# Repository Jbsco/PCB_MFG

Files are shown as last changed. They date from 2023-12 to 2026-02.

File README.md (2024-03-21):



# PCB_MFG

This repository was created for working with and improving the on-campus PCB design and production process using open-source software resources as well as physical resources and space provided by the University of Colorado Boulder and Colorado Mesa University Partnership Program on the Colorado Mesa University campus. These resources are made available to students and faculty alike.

## Introduction

PCB production is in the process of being made more accessible to students and faculty. Desktop CNC machines are available in labs at Confluence Hall which have the capacity to produce good quality single-sided designs, as well as double-sided designs (with some additional effort), with low/no cost for students and faculty. Efforts have been made to reduce complexity and improve ease-of-use by developing a consistent and repeatable process that produces usable results in a shorter time-frame than ordering from third-party prototyping services.

## Participation

Student and faculty participation in this repository is encouraged! Please check the  and <a href="../../issues">Issues</a> pages to learn about proposed changes and additions. Your engagement in development of this process is welcome. Feedback is also appreciated!
A great way to get started with new commits is to fork this repository, make your changes, and create a pull request to merge changes back into the main branch (pending approval). [Workflow actions](https://github.com/Jbsco/PCB_MFG/actions) are enabled to help enforce spell checking, this uses the [Check-Spelling](https://github.com/marketplace/actions/check-spelling) action.

## Hardware Used

The CNC machines located in Confluence Hall labs are being made available for specific projects by faculty permission, and may be made more widely available in the future. Discuss access with faculty and ensure thorough understanding of the equipment, materials, and lab policies before use - you will gain valuable assistance and knowledge to improve your results and ensure that these resources remain effective and safe for use.

### Genmitsu 3018 Pro Desktop CNC Machines

A 3D-printable fixture which fits 100x70mm copper-clad boards is provided as an STL file in this repository. This was designed specifically for this CNC machine and this process. It provides an easy clamping method with consistent repeatability.

<p align="center">
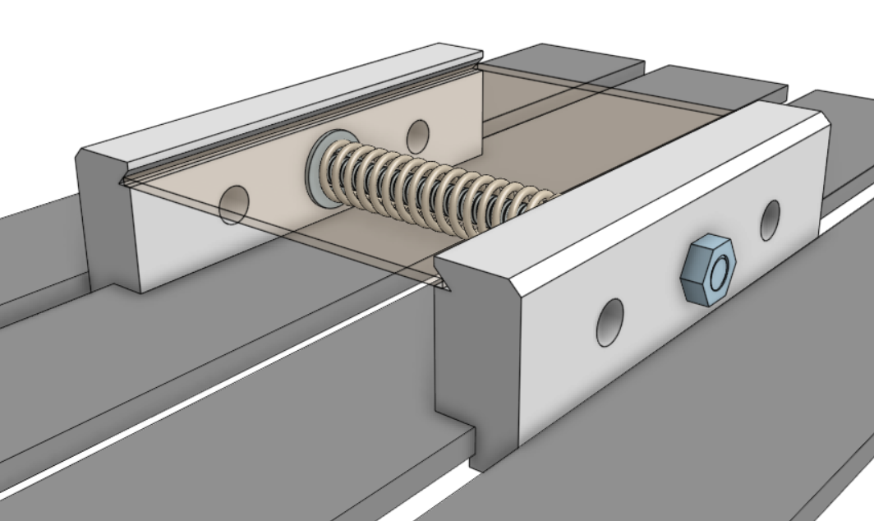
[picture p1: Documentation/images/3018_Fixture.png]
100x70mm Fixture Design
  
</p>

## Software Used

The following software is available on GitHub or their respective web sites, and each were found to be effective for each part of the process detailed within this repository. System compatibility and ease-of-use were priorities, as was open-source status.

* [**Candle**: CNC control and heightmapping software (Windows or Linux)](https://github.com/Denvi/Candle)

* **FlatCAM**: Gerber & Excellon intake, toolpathing, and Gcode output (Windows, Linux, MacOSX) ***comprehensive alternative to Inkscape & jscut***
  * [FlatCAM BitBucket](https://bitbucket.org/jpcgt/flatcam/src/master)
  * [FlatCAM Docs](http://flatcam.org)

* **KiCAD**: Schematic & PCB design software, simulation, Gerber & SVG output (Docker, Windows, Linux, MacOSX)
  * [KiCAD GitHub](https://github.com/KiCad)
  * [KiCAD GitLab](https://gitlab.com/kicad)

Originally, Inkscape and jscut were used to create Gcode files using SVGs, rather than Gerber files. This tested poorly among students, so FlatCAM is preferred, but this process is retained below the current process for posterity.

* **jscut**: SVG intake, toolpathing, and GCode output (in-browser)[
  * [jscut GitHub](https://github.com/tbfleming/jscut)
  * [jscut](https://jscut.org) 
* [**Inkscape**: SVG preparation for jscut (Windows, Linux, MacOSX) ](https://github.com/inkscape/inkscape)

## Process

It is recommended to have access to the above software. As they have their own release channels please refer to their documentation. Generally, Candle, FlatCAM, and KiCAD are installed software, and releases are available from their respective sites. Linux installs for common distributions are often available.

Arch Linux users are recommended to install `candle-bin` from the AUR using `yay`, while FlatCAM runs from source using `python FlatCAM.py` after installing dependencies (`python-vispy` 0.7 or lower is needed. FlatCAM can also be installed as `flatcam-git` from the AUR using `yay`, but the dependency `python-svg.path` may need to be installed with the `--mflags "--nocheck"` flags in order to bypass failed tests), and KiCAD is available using `pacman -Syu kicad` and KiCAD libraries using `pacman -Syu --asdeps kicad-library kicad-library-3d`.

Drivers for the 3018 CNC machine may need to be installed for communication through Candle, these may be found on the Sainsmart site.

Additional documentation (including general usage guides, tips, and tricks) for each application used in this process will be linked within this repo.

## Tutorials

* [Using KiCAD](Documentation/using_KiCAD.md)
* [Using FlatCAM](Documentation/using_FlatCAM.md)
* [Using Candle](Documentation/using_Candle.md)

Originally, Inkscape and jscut were used to create Gcode files using SVGs, rather than Gerber files. This tested poorly among students, so FlatCAM is preferred, but this process is retained here for posterity.

* [Using Inkscape and jscut](Documentation/using_Inkscape_JSCut.md)

## Heightmap Modeling
As a Fall 2023 Intro to Probability Theory final project, a dataset was built from Candle heightmaps and various conclusions were drawn from observations and analysis of this data. Data was interpreted using the MATLAB scripts included in this repository. The resultant report and supporting materials are included in [Reports](/Reports/).

The resultant model heightmap, which is based on the mean data, is available at [/Reports/Code/bootModel.map](/Reports/Code/bootModel.map). This heightmap may prove more useful as the dataset grows.

In the future, other students and faculty will have the opportunity to contribute to the dataset and assist in refining the model.

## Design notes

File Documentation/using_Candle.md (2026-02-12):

# Using Candle

Candle controls the CNC machine directly over USB or by generating a Gcode file for running on a USB stick inserted in the CNC machine.

* Ensure Candle is connected to the CNC machine over USB by selecting "Service → Settings" and "Connection" in the pop-up window. The "Connection" drop-down should show a numbered COM option corresponding to the CNC machine - if not, verify the correct drivers have been installed.

* Close this window and observe the control panel, which may be configured by adjusting settings.
The 3018 Pro CNC machine is capable of making use of the probe and heightmap functions in Candle, which are critical to producing good quality PCB designs.

* In order to use the continuity probe, where the cutting tool making contact with the PCB surface triggers the probe stop, GRBL commands must be sent to the machine via the command terminal, and the tool head spindle must be connected to a "GND" pin on the control board, and the PCB must be connected to the "A5" pin on the control board. Some 3018 Pro machines shipped with different labelling on the control board - the pins may also be labeled "probe". Both types of control boards are present in the campus labs, so please be aware of this if you use different machines. These connections are easily made using alligator clips and pin headers. These connections must be removed when turning the spindle on - **be sure to always check and check again that these clips are removed from the spindle before turning the spindle on**.

* The GRBL commands that must be sent to properly set the homing cycle for continuity probing are `$22=1` (homing cycle enable) and `$23=0` (homing cycle direction). Additional GRBL commands are provided in the "GRBL_Settings_Pocket_Guide_Rev_B" document or at www.DIYMachining.com/GRBL.

* With the homing cycle configured, spindle off, and clips attached, use the control panel to raise the tool head and position the cutting tool over a corner of the PCB. Note the directionality of all controls, and observe the Candle graphical display of the tool head.

* The Z-probe button may be used to slowly lower the tool head until continuity is made and the tool head stops. Zero the machine in Candle by selecting the Zero X, Y, and Z buttons in the control panel.

* Load the Gcode file generated by FlatCAM by selecting "File → Open". Select the contour CNC job.

<p align="center">
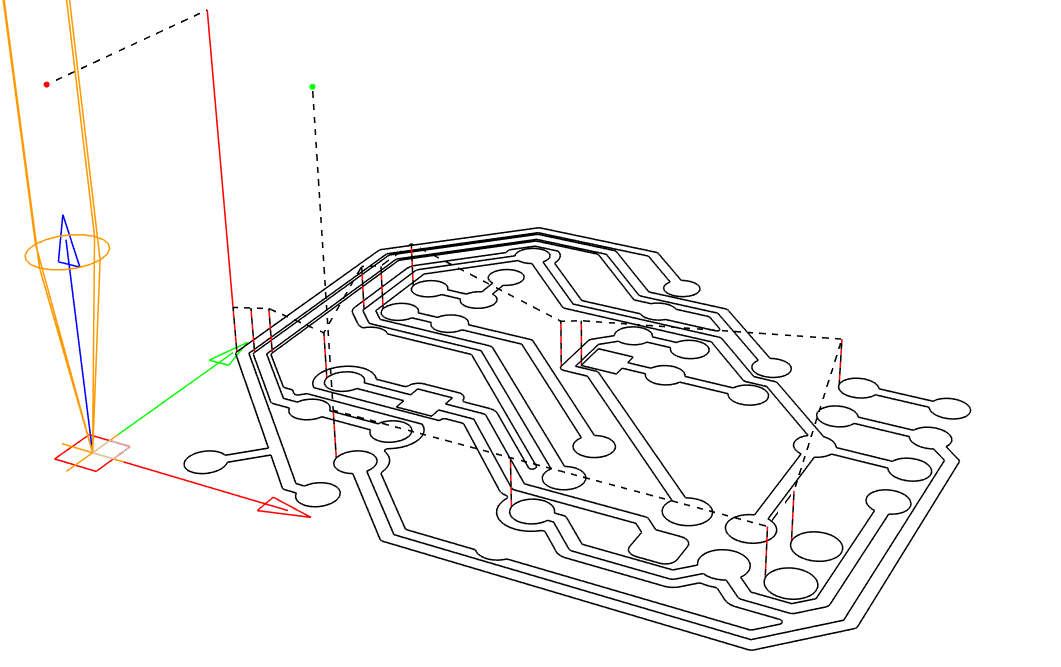
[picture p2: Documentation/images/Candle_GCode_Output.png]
Example Gcode File Loaded in Candle
  
</p>

* Once a Gcode file is opened, Candle enables the Heightmap function. Select "Create" (or optionally apply the modeled heightmap that was developed for rapid prototyping using the fixture design included in this repository).

* Adjust the Heightmap settings to enclose the design shown in the graphical window, or select the "Auto" button to automatically set parameters.

* Select reasonable values for the Heightmap Probe Grid. Some parameters may be unfamiliar - "F" is the probe feedrate, "Zt" is the distance to raise the tool head when moving to the next point, and "Zb" is the distance to lower the tool head when probing. If the machine was zeroed previously, then a value of 1.50 for Zt with other values left as default is likely sufficient.

* Observe the arrangement of the graphical representation of the operation and visually verify that the machine will not crash before selecting "Probe". The routine will run until complete or stop if continuity was made at an unexpected point. If the Heightmap was not able to be completed, try adjusting the "Zt" or "Zb" parameters accordingly, or inspect for other issues, before trying again.

<p align="center">
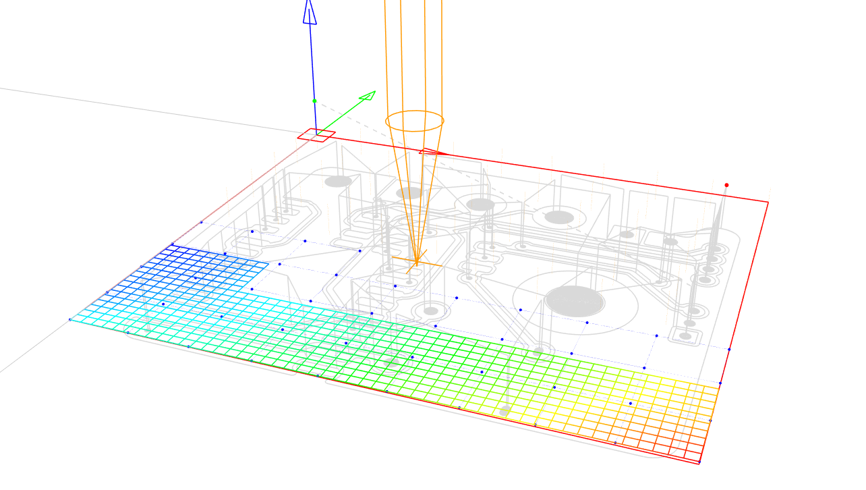
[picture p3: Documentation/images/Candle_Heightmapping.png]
Example Candle Heightmap Routine Being Performed
  
</p>

* With the Heightmap complete, close the Heightmap mode by selecting "Edit", and select the checkbox "Use Heightmap".

* Raise the tool head slightly and reset alarms if necessary.

* Perform additional visual checks to verify the machine will be able to proceed with the milling operation unobstructed, and **remove clips attached to the spindle and PCB before turning the spindle on**.

***Note that the spindle rotates near 10,000 RPM, and the cutting bit could break and create a dangerous situation. Follow lab policies regarding safety and have faculty or senior students familiar with this process verify that everything is in order before turning on the spindle and running milling Gcode.***

* Turn the spindle on and select "Send" to run the operation. Observe the machine safely and while wearing safety glasses.

* The routine should complete and the PCB will be ready for hole drilling operations. Hole drilling operations should be completed without changing the machine zero positioning, or else alignment will be difficult to achieve accurately. The hole drilling operation should be straightforward so long as the tool bit is changed without losing the machine positioning.

<p align="center">
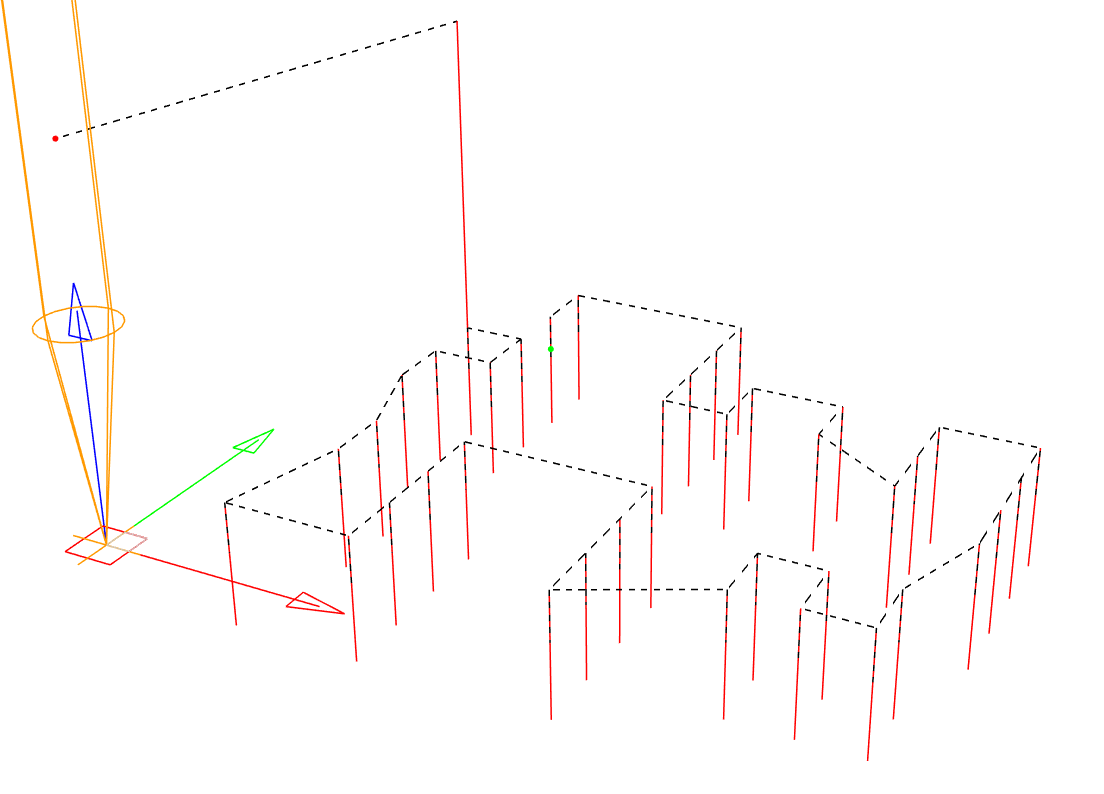
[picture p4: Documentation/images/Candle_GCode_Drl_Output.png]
Example Drill Gcode File Loaded in Candle
  
</p>

The routine should complete and the PCB will be ready for final processing or cutting operations.

<p align="center">
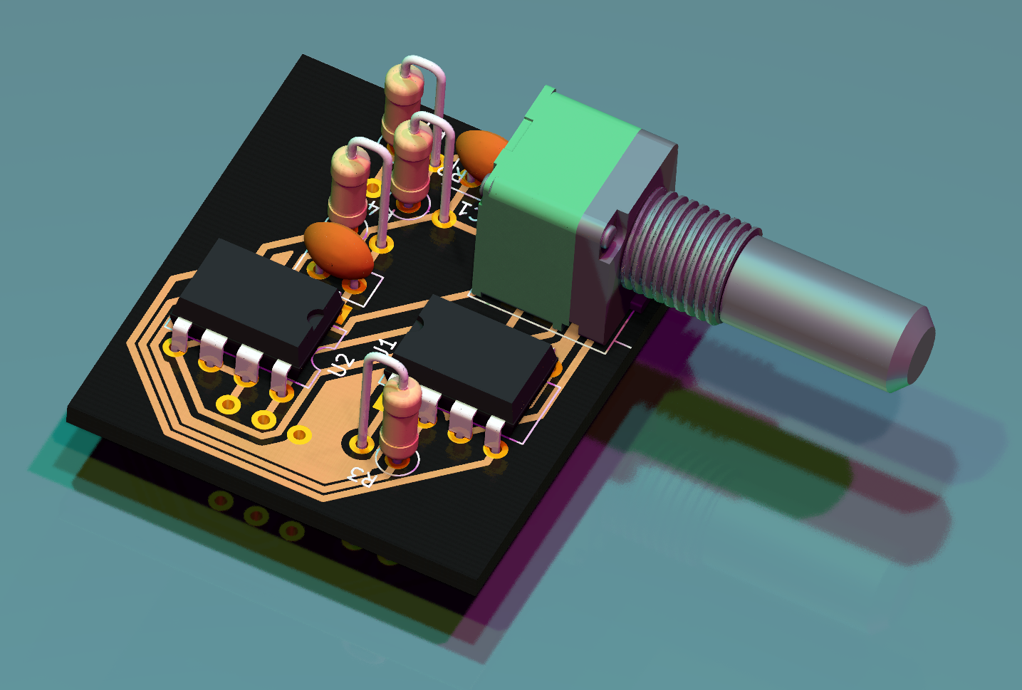
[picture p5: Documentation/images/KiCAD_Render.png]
Example Populated PCB Rendered in KiCAD
  
</p>

Candle Tips (for Genmitsu CNC 3018-PRO): [Tips_Candle_Genmitsu_CNC3018](./using_Candle_GenmitsuCNC3018.md)

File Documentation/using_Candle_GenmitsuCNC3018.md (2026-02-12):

# FlatCAM Tips (for Genmitsu CNC 3018-PRO)

This section provides practical guidelines to reduce common **design and manufacturing issues** when milling PCBs designed in **KiCad** using the **Genmitsu CNC 3018-PRO** CNC machine
([Amazon link](https://www.amazon.com/Genmitsu-3018-PRO-Control-Engraving-300x180x45mm/dp/B07P6K9BL3)).

<p align="center">
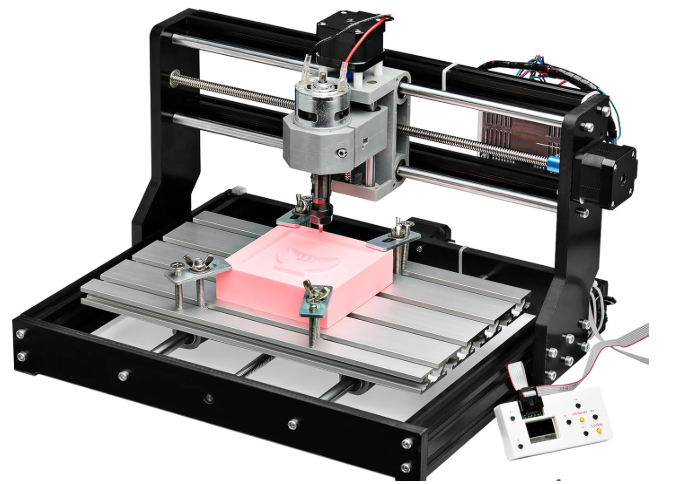
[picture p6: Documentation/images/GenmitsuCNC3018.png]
Genmitsu CNC 3018-PRO
  
</p>

The **Genmitsu CNC 3018-PRO** is an entry-level, desktop, 3-axis CNC router intended for hobbyists, students, and educational environments. It has a working area of approximately **300 × 180 × 45 mm**, uses a 775 spindle motor, and is controlled via **GRBL firmware**.

The machine is commonly used for engraving and light milling of materials such as wood, plastics, acrylic, **PCB copper boards**, and soft aluminum. While affordable and relatively easy to assemble, it is designed for **prototyping and learning**, not industrial-grade PCB manufacturing.

Although the machine offers reasonable precision, PCB milling imposes strict constraints on **trace width, clearance, pad size, and tool depth**. Inadequate settings can easily result in short circuits, broken traces, incomplete isolation, or partially milled pads.

---

# Safety Notes

- Always wear **eye protection**
- Never touch the tool while the spindle is running
- Keep hands away from moving parts

<p align="center">
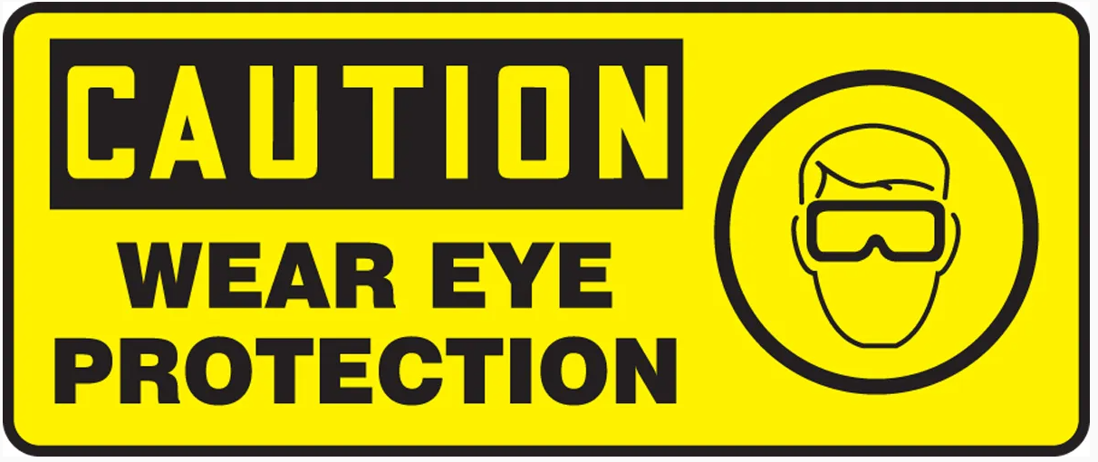
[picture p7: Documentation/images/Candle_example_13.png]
  
</p>

---

# Candle Guidelines for CNC Milling

From **FlatCAM**, three G-code files must be generated:

- `'name'_MILLING_0.075.nc`
  — Used in **Candle** to mill (isolate) the copper traces

- `'name'_DRILLING_0.075.nc`
  — Used in **Candle** to mark the hole centers

- `'name'_DRILLING_2.5.nc`
  — Used in **Candle** to drill the holes through the board

---

# Installing Candle

Download Candle

On Linux, you may need to run:

```bash
sudo ./candle
```

---

# Required Items for This Activity

<p align="center">
  
</p>

- Genmitsu CNC 3018-PRO
- 3D-printable fixture
- USB cable
- Power supply
- Phenolic copper clad board (approx. 10 × 8 cm)
- Milling bit (0.5 mm recommended)
- Drill bit (1.0 mm recommended)
- Z-probe wires (green and white)

---

# Preparing the CNC Machine

- Plug the USB cable into the computer (**do not turn on the CNC machine yet**)
- Open Candle:
  ```bash
  sudo ./candle
  ```

- Ensure the status shows **"Idle"**
  - If not: `Service → Settings → Port`

- Click the **lock button** to unlock the machine
- Press the **emergency button** (so the machine does not move when powered)

<p align="center">
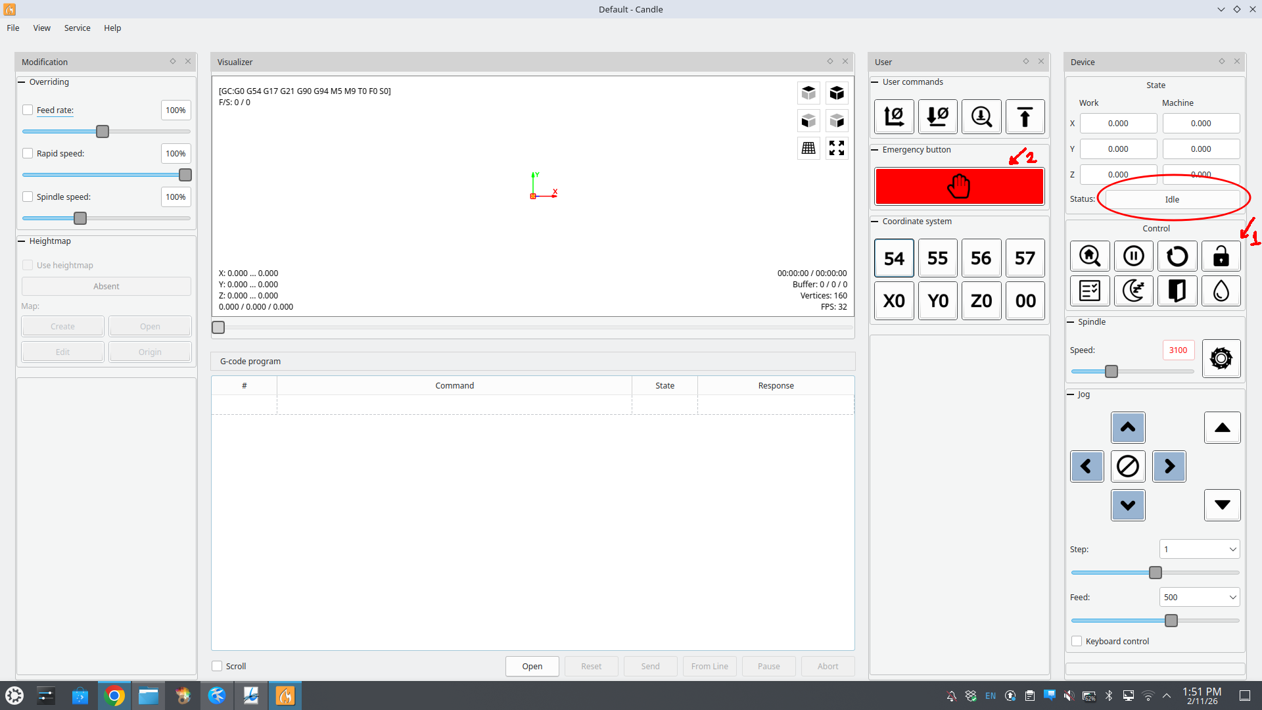
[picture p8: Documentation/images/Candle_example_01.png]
  
</p>

- Plug the CNC machine into the power outlet
  - The machine should NOT move

- Close and Restart Candle

- Ensure status is **Idle**

- Unlock the machine

- You can now move the axes using Candle controls

- Move the spindle to one corner of the machine
  - **Do not exceed machine limits**

- Install the board holder system

<p align="center">
  
</p>

- Place the **phenolic copper clad sheet (10 × 8 cm)**

<p align="center">
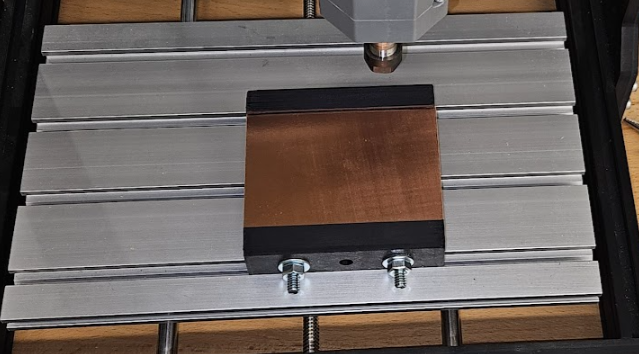
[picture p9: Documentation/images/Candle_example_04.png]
  
</p>

---

# Preparing the Tools

To maintain consistent tool height, mark both tools at the same reference height.

### Tools

- **Milling tool:**
  0.5 mm carbide end mill (1/8" shank)

- **Drilling tool:**
  1.0 mm tungsten carbide PCB drill bit (1/8" shank)

<p align="center">
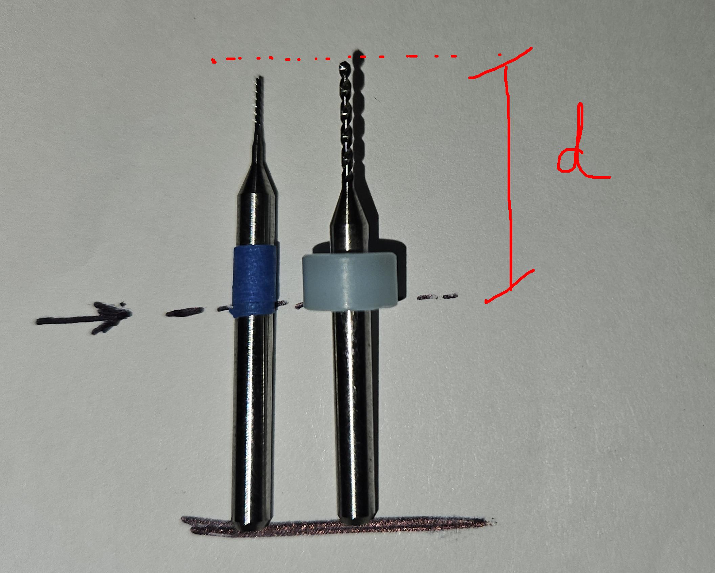
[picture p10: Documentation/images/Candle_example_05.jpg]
  
</p>

- Install the **milling tool** first

---

# Setting the XY Reference (Origin)

- Close and Restart Candle

- Ensure status is **Idle**

- Unlock the CNC machine

- Move the spindle to the **bottom-left corner of the copper board**

<p align="center">
  
</p>

- Set this position as **X = 0, Y = 0**

<p align="center">
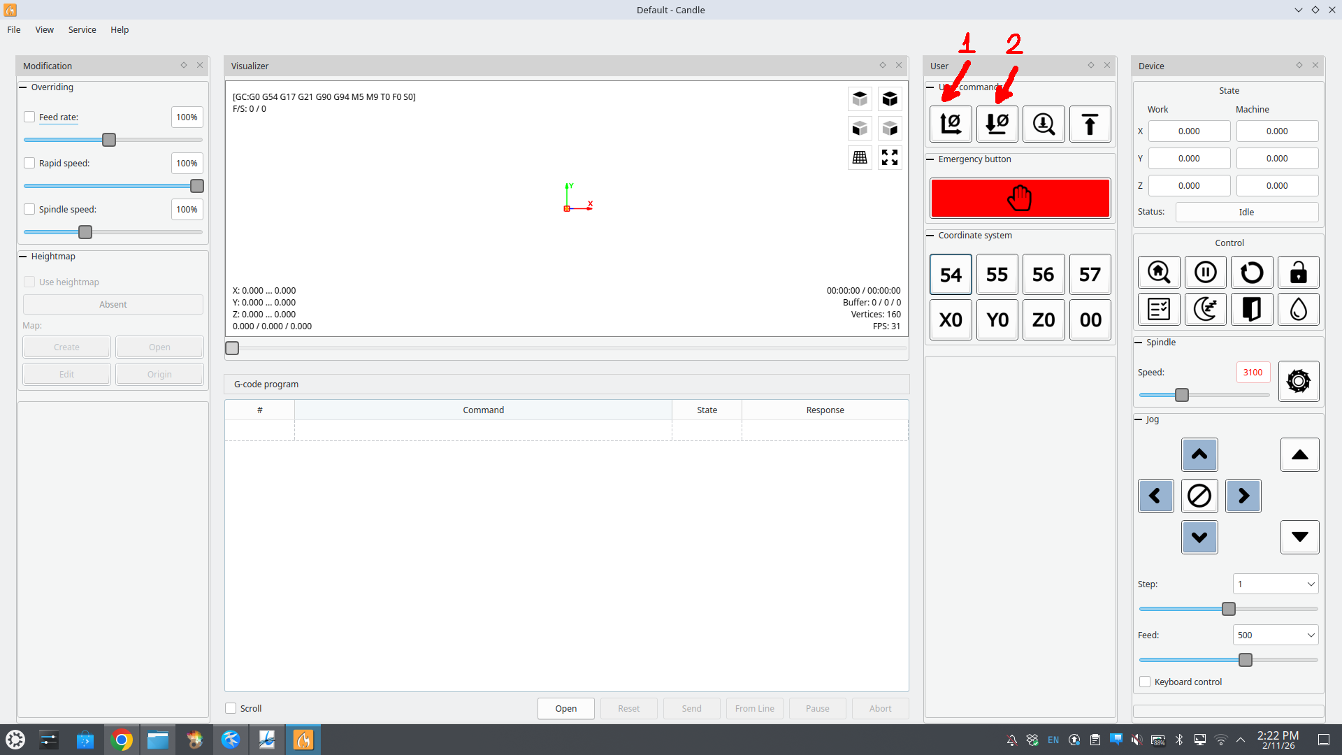
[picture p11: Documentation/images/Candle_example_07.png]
  
</p>

- Close and Restart Candle

- Ensure status is **Idle**

- Unlock the CNC machine

- Set this position as **X = 0, Y = 0** again

- Load the milling file:
  `'name'_MILLING_0.075.nc`

- Set **Safe Z**

⚠ **If the spindle moves unexpectedly, immediately turn off the machine.**

<p align="center">
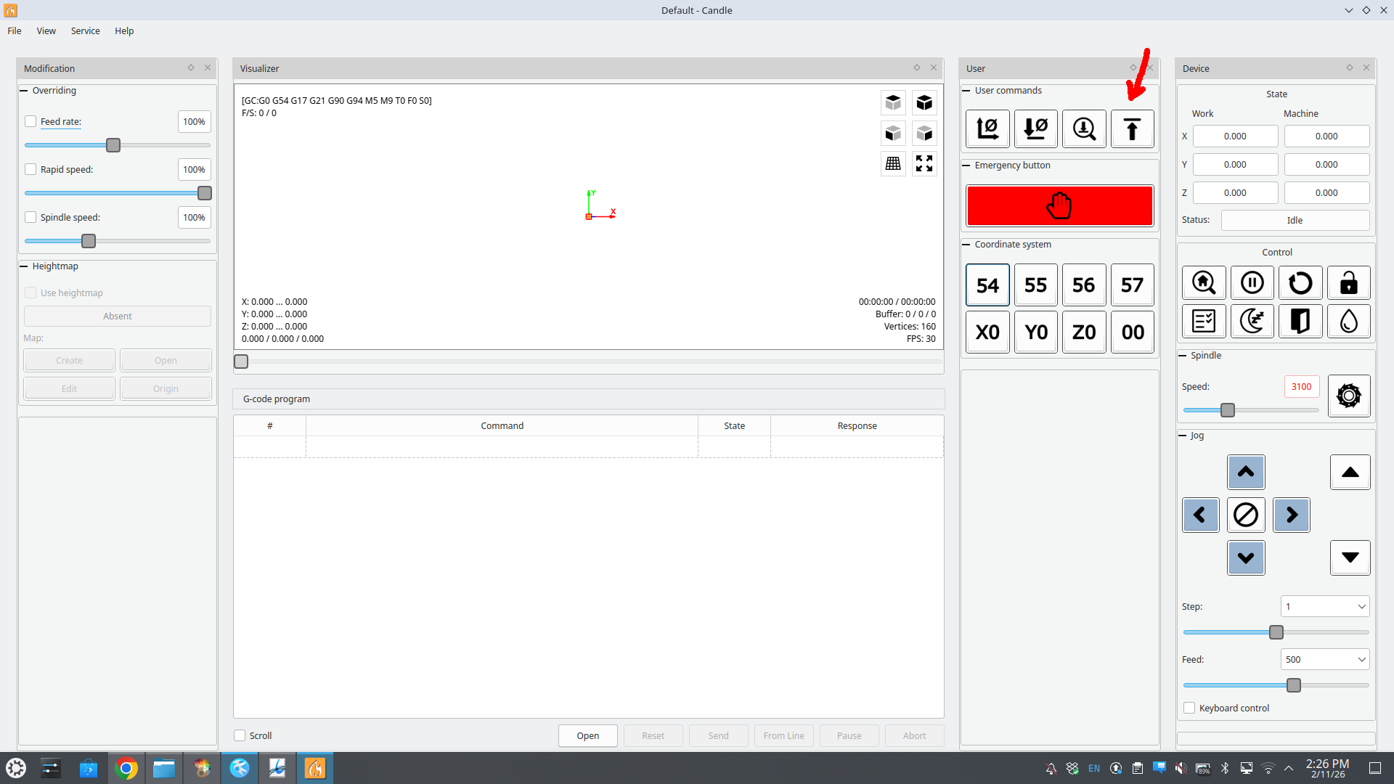
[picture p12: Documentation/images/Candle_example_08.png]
  
</p>

---

# Setting the Z-Probe

Before probing:

- Ensure the two probe cables are connected properly

<p align="center">
  
</p>

- For this setup:
  - **White cable → spindle motor**
  - **Green cable → copper board**

<p align="center">
  
</p>

⚠ **WARNING:**
Improper connection may damage the board or tool.

- Click **PROBE Z**

<p align="center">
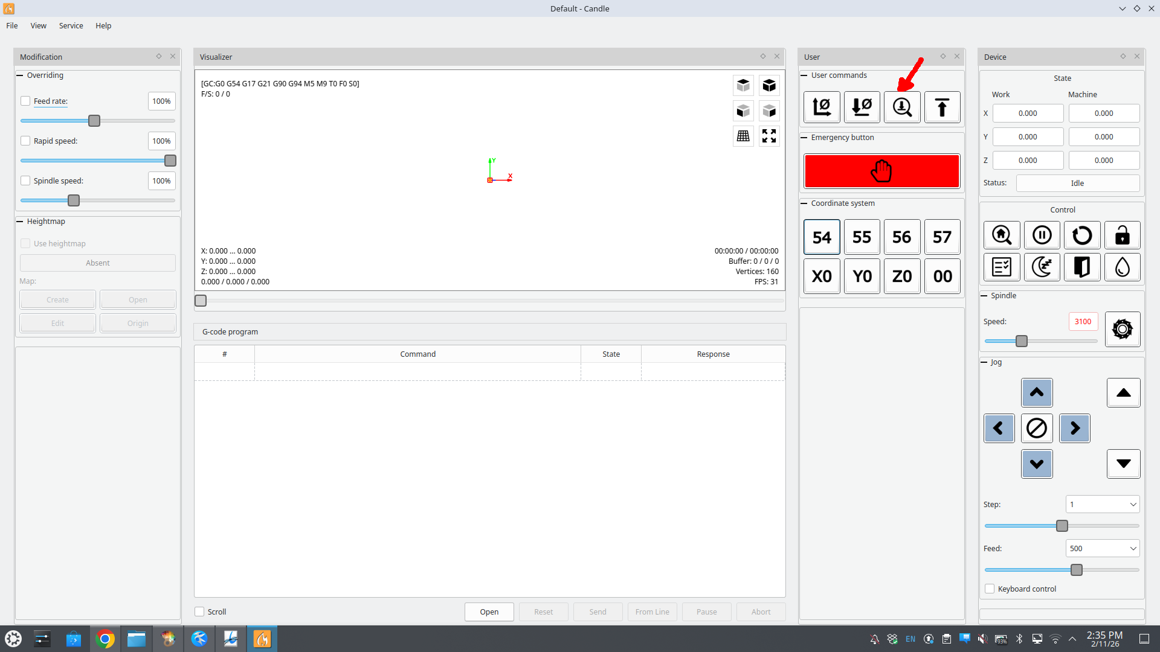
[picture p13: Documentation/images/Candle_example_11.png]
  
</p>

---

# Creating the Heightmap

- Click **Create**
- Click **Auto** (covers only the board area)
- Set:
  - **Zt = 2** (safe probing height)
  - **Zb = -1** (maximum probing depth)

<p align="center">
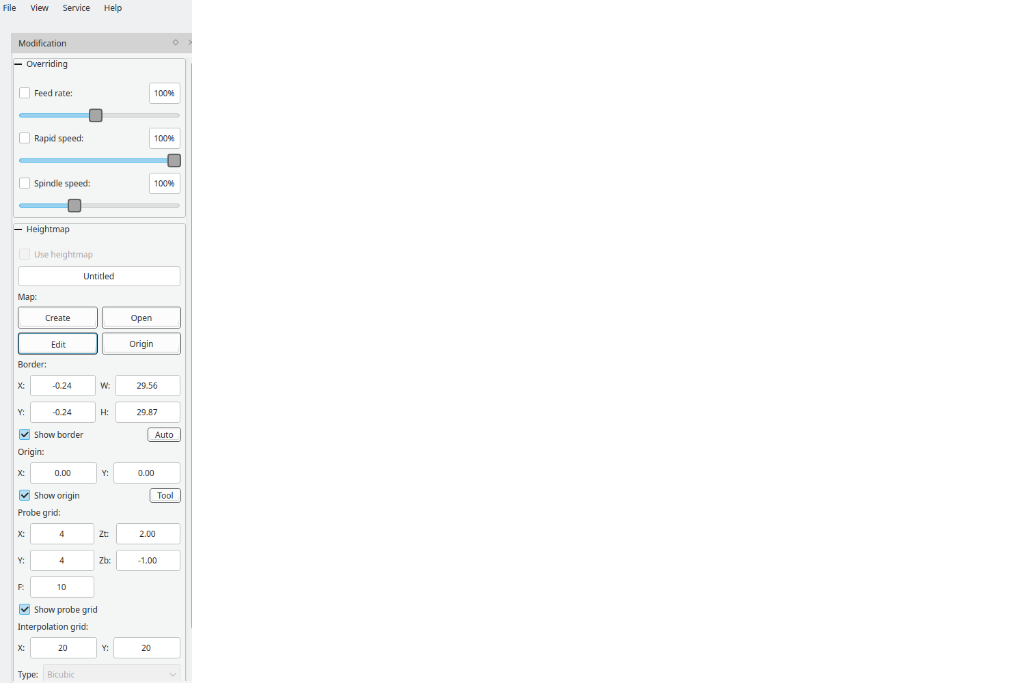
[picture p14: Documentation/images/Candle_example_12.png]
  
</p>

- Click **PROBE**
- When finished, click **EDIT** to return to the main screen

⚠ **Disconnect the white and green probe wires before proceeding**

---

# Using the Heightmap

- Enable **Use Heightmap**

- Set spindle speed (**FEED**) to **3000 rpm**

⚠ Double-check that probe wires are disconnected

- Click **SEND**

The milling process will now begin using surface compensation from the heightmap.

---

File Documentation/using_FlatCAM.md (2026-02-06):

# FlatCAM

* In FlatCAM, open the Gerber and the Excellon files to add them to the FlatCAM project.

<p align="center">
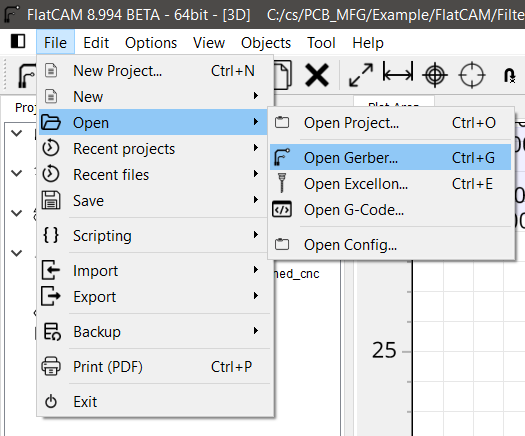
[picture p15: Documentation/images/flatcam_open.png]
FlatCAM Open Dialogue
  
</p>

* These objects may be placed far from the origin, so select all using the "Ctrl + A" shortcut, and Move to Origin using the "Shift + O" shortcut. It is important to select all objects to move them as a group, otherwise the drill objects will not be aligned to the contour objects.

<p align="center">
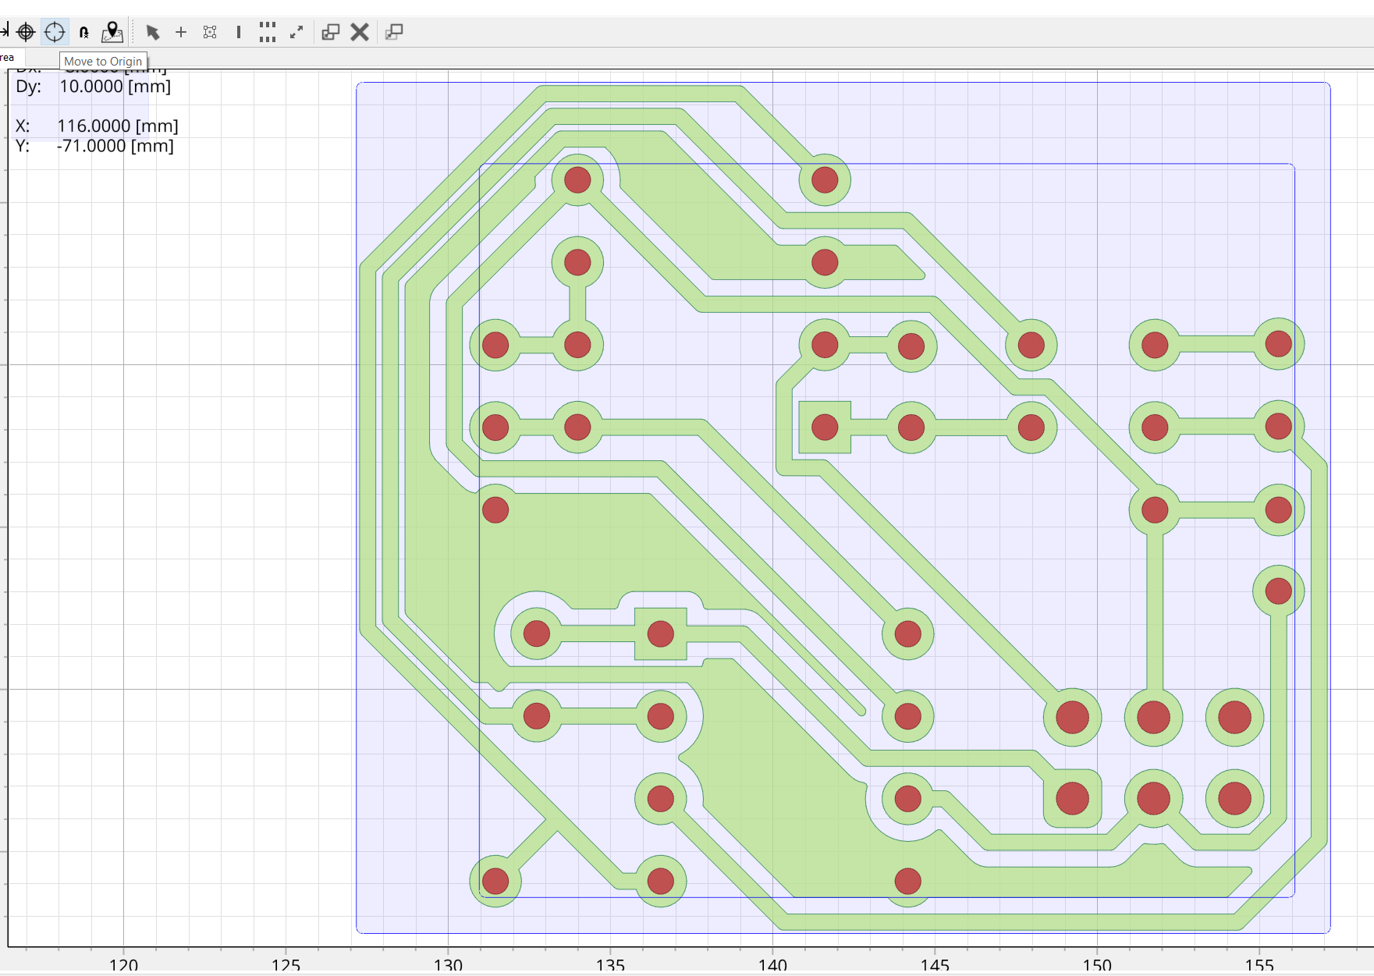
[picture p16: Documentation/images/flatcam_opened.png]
FlatCAM Opened Objects
  
</p>

## Generating Trace GCode

* Double-click the Gerber in the project tree side panel, then select "Isolation Routing".

<p align="center">
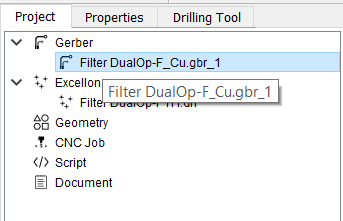
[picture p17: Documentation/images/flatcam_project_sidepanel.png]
FlatCAM Side Panel
  
</p>

* Right click the #1 tool in the Tools Table and delete it. We must set up a new tool to mill at the 0.1mm depth of cut using the lab's V-cutter bits.

* Use the "Ctrl + D" shortcut to open the Tools Database. You may create a new tool here, but it is recommended to import the database provided in this repository. Select "Import DB" and select the [Tools_Data_Base.TXT](../FlatCam_Tools_Database/Tools_Data_Base.TXT) file to import the V-cutter tool.

* Select "Pick from DB" in the sidebar, select the "V-Cutter" tool, and select "Transfer the Tool" to apply to the Isolation Tool operation.

* Change "Tool Dia." to match the 0.0354 diameter, and select "Generate Geometry".

* Change the Preprocessor to 'grbl_11_no_M6', followed by "Generate CNCJob Object".

<p align="center">
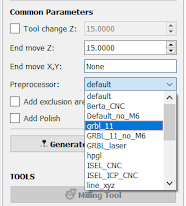
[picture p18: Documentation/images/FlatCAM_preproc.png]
FlatCAM Preprocessor
  
</p>

* The contour job is complete, select "Save CNC Code" or right click the CNC Job in the project tree side panel to save the Gcode for access with Candle later.

## Generating Drill GCode

* The drill job can now be created. This operation may vary depending on your requirements. For example, the provided design uses two different size vias, and these can either be combined to one size or retained as two different drill operations. Depending on drill bit availability and prototyping requirements, you may opt to simplify this operation to use the smallest size drill, otherwise it is recommended to use the Tool Change option to provide for drill changing.

* Double click the Excellon drill file in the project tree side panel, and select "Excellon Editor" to make changes to the drills this operation will apply to. For example, edit all sizes to the same value to combine drills.

<p align="center">
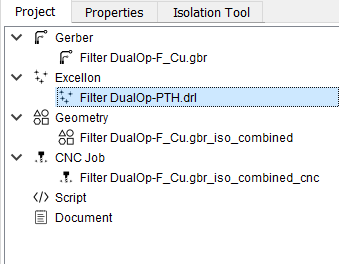
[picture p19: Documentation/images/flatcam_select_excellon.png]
FlatCAM Excellon in Side Panel
  
</p>

<p align="center">
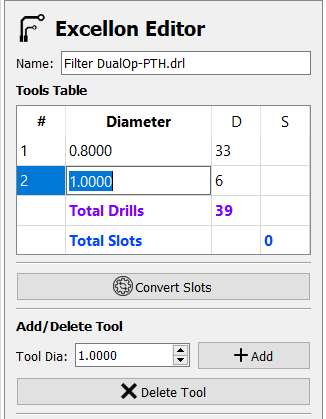
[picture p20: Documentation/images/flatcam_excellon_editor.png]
FlatCAM Excellon Editor
  
</p>

* Exit the editor and save changes. Select "Drilling Tool" and edit parameters accordingly. Since this is a separate operation from the contour, it will be critical that the CNC machine retains its positioning to ensure alignment. Keep this in mind when setting parameters for tool changes, if this option is selected.

* It is recommended to reduce Feedrate Z to 60 (300 may be too high and could cause damage to the board). Adjust Cut Z to a value that will completely drill through the board. If using the provided fixture, there will be ample clearance under the board.

* Select "Generate CNCJob Object" and save in the same manner as the contour operation.

<p align="center">
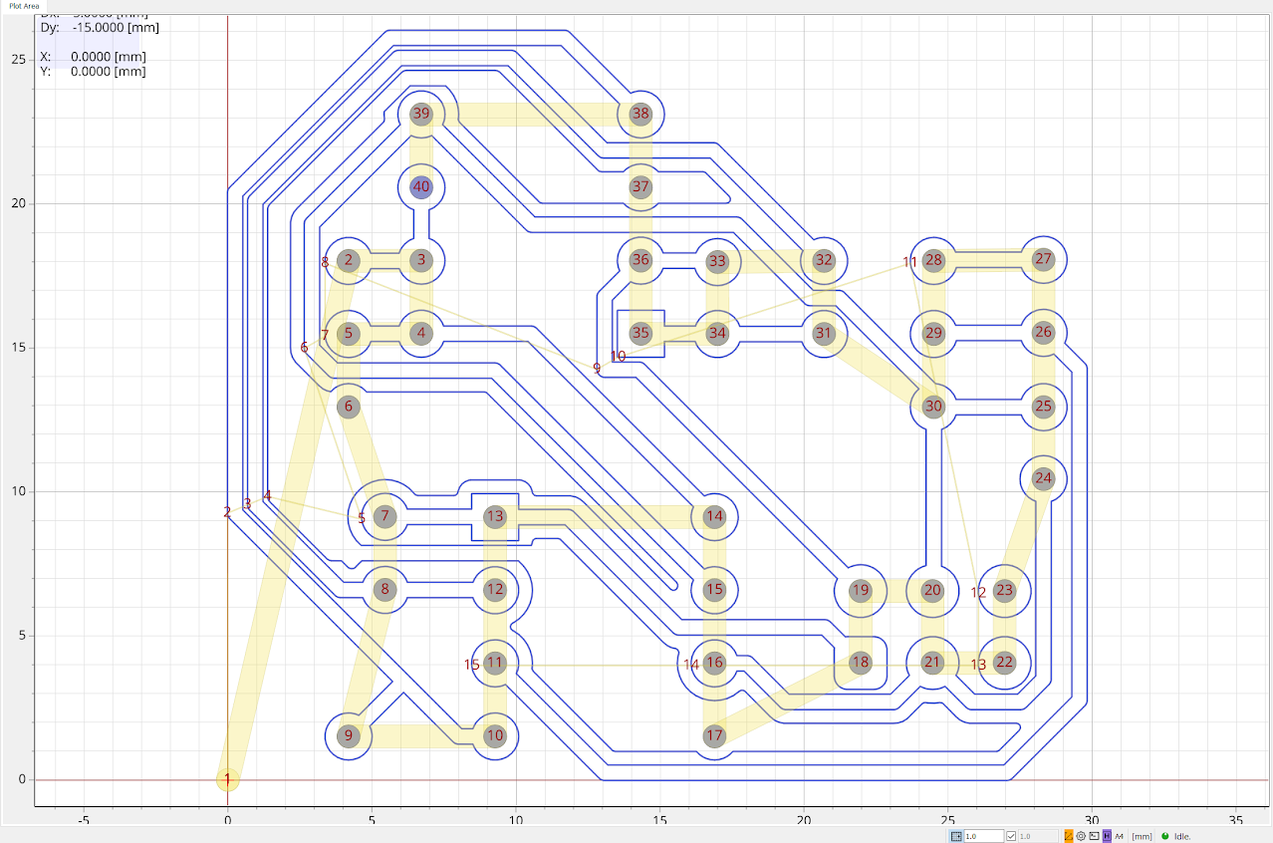
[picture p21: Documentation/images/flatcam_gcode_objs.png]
FlatCAM CNC Jobs
  
</p>

These Gcode files may be opened directly in Candle for heightmap generation and running the machine.

FlatCAM Tips Instalation (Linux): [Tips_FlatCAM_Linux](./using_FlatCAM_Linux.md)

FlatCAM Tips (for Genmitsu CNC 3018-PRO): [Tips_FlatCAM_Genmitsu_CNC3018](./using_FlatCAM_GenmitsuCNC3018.md)

→ Next Tutorial: [Using Candle](./using_Candle.md)

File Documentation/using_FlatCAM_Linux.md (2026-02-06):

# FlatCAM Tips (Linux)

This section describes how to **install and run FlatCAM on Linux** using the FlatCAM Beta repository and a Python virtual environment.

---

## Cloning the FlatCAM Repository

- Clone the FlatCAM Beta repository:
git clone https://bitbucket.org/marius_stanciu/flatcam_beta.git

- Navigate into the project directory:
cd flatcam_beta

- Checkout the recommended FlatCAM version:
git checkout Beta_8.995

---

## Python Virtual Environment Setup

- Create a Python 3 virtual environment:
python3 -m venv ~/flatcam-venv

- Activate the virtual environment:
source ~/flatcam-venv/bin/activate

---

## Installing Dependencies

- Edit the `requirements.txt` file and comment out libraries that may fail to install (for example, `gdal`).

- If installation fails, a recommended approach is:
  - Comment out **all** libraries
  - Uncomment **one library at a time**
  - Run the installer and check for errors

- Install the remaining dependencies:
pip install -r requirements.txt

---

## Running FlatCAM

- Activate the virtual environment:
source ~/flatcam-venv/bin/activate

- Launch FlatCAM:
python3 flatcam.py

---

## Known Bug Fix (Laser / Spindle Code)

If FlatCAM **opens and immediately closes**, apply the following fix.

- Open the file:
camlib.py

- Locate approximately line **3866** and replace:

      `# self.laser_on_code = tool_dict['tools_mill_laser_on']`

      self.laser_on_code = "M03"

This forces FlatCAM to use the correct spindle enable command for **GRBL-based CNC controllers**, including the **Genmitsu CNC 3018-PRO**.

---

## Running FlatCAM (After Installation)

- Activate the virtual environment:
source ~/flatcam-venv/bin/activate

- Start FlatCAM:
python3 flatcam.py

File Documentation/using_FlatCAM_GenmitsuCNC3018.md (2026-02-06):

# FlatCAM Tips (for Genmitsu CNC 3018-PRO)

This section provides practical guidelines to reduce common **design and manufacturing issues** when milling PCBs designed in **KiCAD** using the **Genmitsu CNC 3018-PRO** CNC machine
([Amazon link](https://www.amazon.com/Genmitsu-3018-PRO-Control-Engraving-300x180x45mm/dp/B07P6K9BL3)).

<p align="center">
  Genmitsu CNC 3018-PRO
</p>

The **Genmitsu CNC 3018-PRO** is an entry-level, desktop, 3-axis CNC router intended for hobbyists, students, and educational environments. It has a working area of approximately **300 × 180 × 45 mm**, uses a 775 spindle motor, and is controlled via **GRBL firmware**. The machine is commonly used for engraving and light milling of materials such as wood, plastics, acrylic, **PCB copper boards**, and soft aluminum. While affordable and relatively easy to assemble, it is designed for **prototyping and learning**, not industrial-grade PCB manufacturing.

Although the machine offers reasonable precision, PCB milling imposes strict constraints on **trace width, clearance, and pad size**. Inadequate values can easily result in short circuits, broken traces, or partially milled pads.

---

## FlatCAM Design Guidelines for CNC Milling

From KiCAD, two fabrication files must be generated:

- `'name'_B_Cu.gbr` — Gerber file containing the copper traces
- `'name'_PTH.drl` — Excellon drill file containing the hole locations

### Loading Files in FlatCAM

- Open **FlatCAM**
- Load the fabrication files:
  - `File → Open → Open Gerber` → select `'name'_B_Cu.gbr`
  - `File → Open → Open Excellon` → select `'name'_PTH.drl`

### Move the Board to the Origin

- Select all objects: **Ctrl + A**
- Go to `Edit → Move to Origin`

### Mirror the Board (Required for Bottom Layer)

- Select all objects: **Ctrl + A**
- Go to `Options → Flip on X-axis`

---

## Preparing the MILLING File from Gerber (`'name'_B_Cu.gbr`)

- Double-click the Gerber file in the project tree

<p align="center">
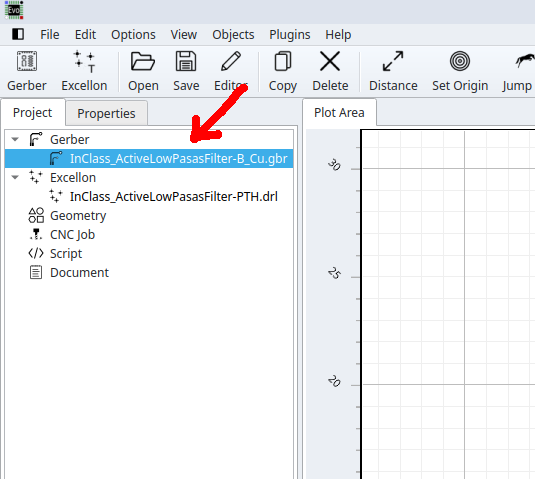
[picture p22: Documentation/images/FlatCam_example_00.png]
  
</p>

- Open **Isolation Routing**
- Click **Beginner** to switch to **Advanced** mode
- Remove tool **#1 (Diameter)**
  *(Right-click → Delete)*

- Click **Pick from DB** to select a tool
- Open **Settings**
  - **Diameter:** `0.475 mm`
  - **Cut Z:** `-0.075 mm`

<p align="center">
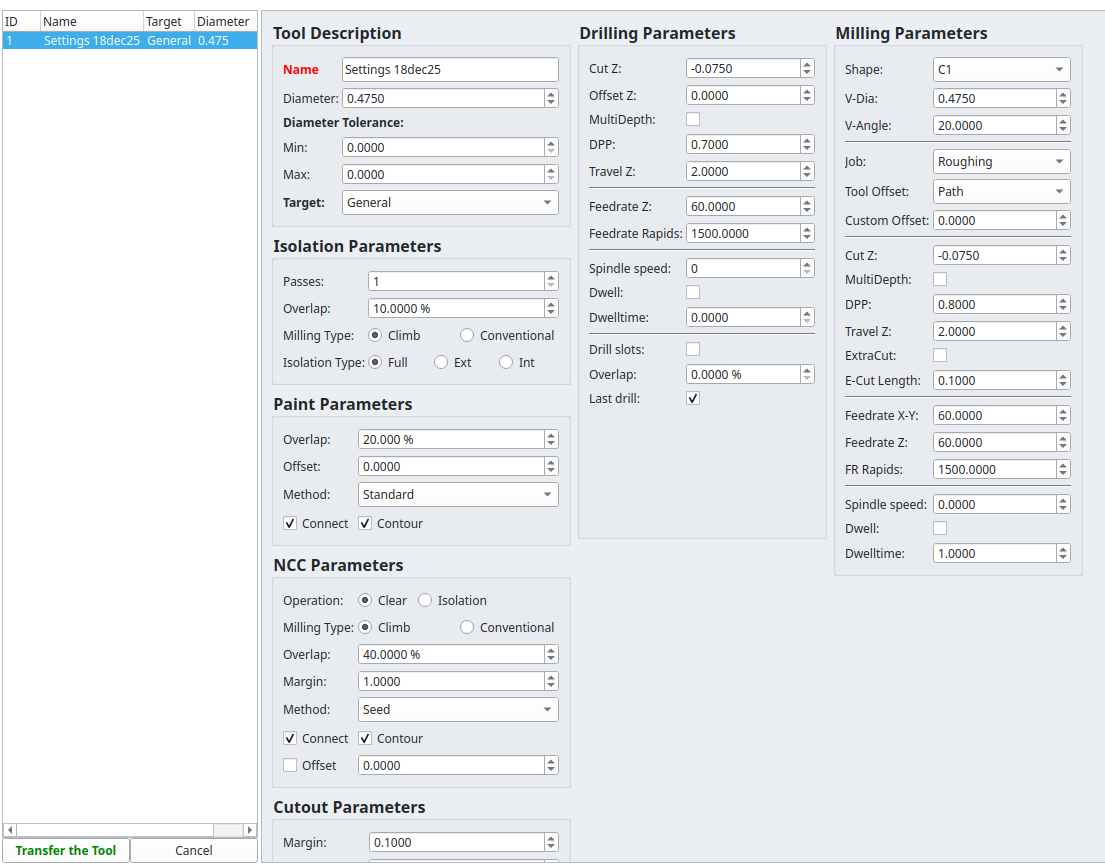
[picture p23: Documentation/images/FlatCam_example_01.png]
  
</p>

- Click the tool, then click **Transfer Tool**

<p align="center">
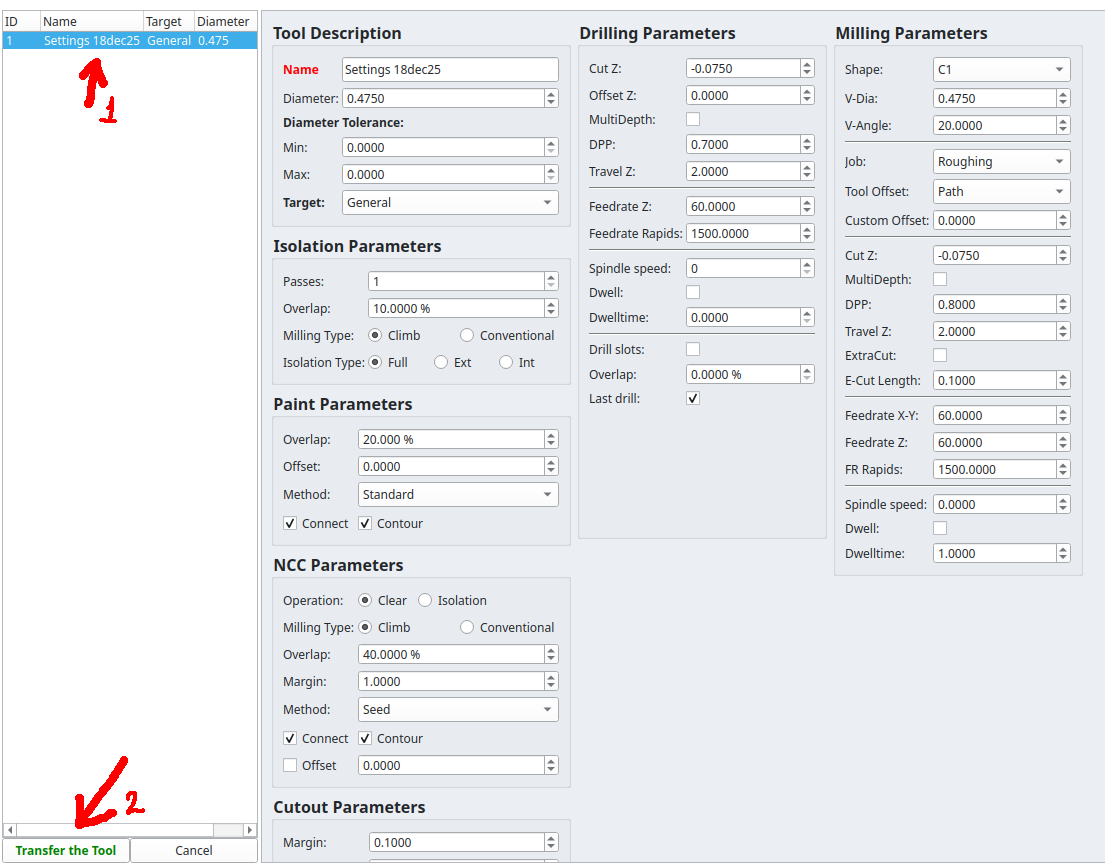
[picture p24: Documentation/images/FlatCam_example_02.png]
  
</p>

- Click **Generate Geometry**

A confirmation message should appear in the bottom-left corner, and the generated toolpath should become visible:

<p align="center">
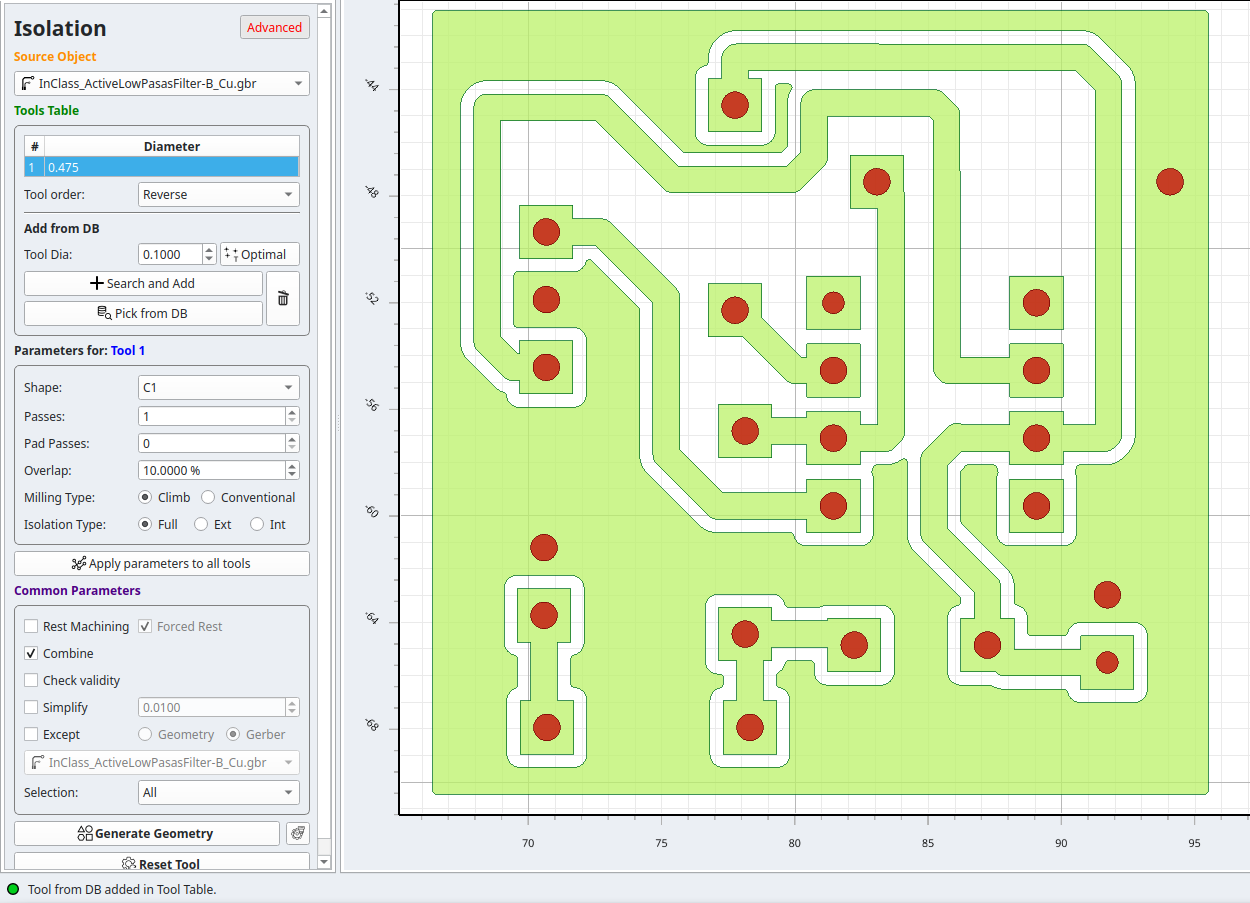
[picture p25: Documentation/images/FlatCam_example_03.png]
  
  
</p>

---

## Generating the CNC Job (Milling)

- Select the **Milling** geometry object

<p align="center">
  
</p>

- Configure the CNC job parameters:
  - **Cut Z:** `-0.075 mm`
    *(Depth of cut relative to the Z reference)*

  - **Travel Z:** `2.0 mm`
    *(Safe height when moving between cuts)*

  - **Postprocessor:** `GRBL_11_no_M6`

<p align="center">
  
</p>

- Click **Generate CNC Job Object**

<p align="center">
  
</p>

### Saving the File

- Save the CNC job file as:
  'name'_**MILLING_0.075**.nc

---

## Preparing the DRILLING Files from Excellon (`'name'_PTH.drl`)

### Drill Center Marking File

- Go to the **Project** tab
- Double-click the `.drl` file in the project tree

<p align="center">
  
</p>

- Open **Excellon Editor**
- Change the diameter of **all holes** to `1.0 mm`
- Exit the editor → **Yes**
- Click **Drilling**
- **Settings**

<p align="center">
  
</p>

- Click **Generate CNC Job Object**

### Saving the File

- Save the CNC job file as:
  'name'_**DRILLING_0.075**.nc

**Note:** This file is used **only to mark the center of the holes**.

---

### Drill Through-Hole File

- Go **BACK** to the **Project** tab
- Double-click the `.drl` file in the project tree

<p align="center">
  
</p>

- Open **Excellon Editor**
- Change the diameter of **all holes** to `1.0 mm`
- Exit the editor → **Yes**
- Click **Drilling**
- Open **Settings**
  - Change **Cut Z** to `-2.5 mm`

<p align="center">
  
</p>

- Click **Generate CNC Job Object**

### Saving the File

- Save the CNC job file as:
  'name'_**DRILLING_2.5**.nc

**Note:** This file is used to **fully drill the holes**.

---

## Generated G-code Files Summary

From FlatCAM, **three files** must be generated:

- 'name'_**MILLING_0.075**.nc
  — Used in **Candle** to mill the copper traces

- 'name'_**DRILLING_0.075**.nc
  — Used in **Candle** to mark the hole centers

- 'name'_**DRILLING_2.5**.nc
  — Used in **Candle** to drill the holes through the board

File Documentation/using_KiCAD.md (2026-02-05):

# Using KiCAD
Designs start in a KiCAD project. It is possible to start immediately within the PCB editor, however there are advantages to working within a project file and creating a schematic first.

The schematic editor looks and functions similarly to SPICE software, with usability improvements as well as functionality beneficial to full-stack design work. Components may be added to the KiCAD library, but the existing library is sufficient for intermediate designs. Components can be assigned a footprint, which also often includes a 3D model for rendering visuals and checking 3D space conflicts. Python script support extends functionality and allows for some automation, but is not necessary to produce competent results.

<p align="center">
  Example Schematic Design in KiCAD
</p>

The PCB board editor can be entered from the schematic editor. The two documents are linked, and components in the schematic will be inserted into the board editor as footprints. Use the hotkey "F8" or select "Tools → Update PCB from Schematic", this will place missing footprints. Circuit nets are also shared between the documents. It is possible to auto-place footprints, but it is recommended to manually adjust and rotate components accordingly to make routing easier. The board editor has many layers to manipulate. Most important for prototyping purposes are the top copper layer and the edge cuts layer. The bottom layer and multiple layers beyond this are also accessible (board stackup settings may be edited at any time). Additional vias and PCB specific components that are not typically present on a circuit schematic can be placed in the same manner as in the schematic editor, with a large default library to explore. Pin headers, I/O vias and pads, connectors, and even active trace elements such as Bluetooth or tuned antennae are present and waiting for application in student projects!

<p align="center">
  Circuit Board Design in KiCAD
</p>

Once a board design is ready to export, _the process will diverge depending on whether you are ingesting **gerber fabrication files with FlatCAM**, or **SVG files with Inkscape and jscut**. Both are effective for prototyping, though the SVG method tested poorly among students. If you opt to go this route, export your copper layer in color, select only the board area, and include edge cuts if you need those outlined in the milling operation. Otherwise, select "File → Fabrication Outputs → Gerbers" and select the layer you are working with. Default settings were found to work well. Select "Plot to create the Gerber file, and then select "Generate Drill Files" (being sure "Drill Units" is set to millimeters) to create the drill Excellon file. Default settings here were also found to work well. Several files are created, however we will only use two in FlatCAM.

KiCad Tips (for Genmitsu CNC 3018-PRO): [Tips_KiCAD_Genmitsu_CNC3018](./using_KiCAD_GenmitsuCNC3018.md)

→ Next Tutorial: [Using FlatCAM](./using_FlatCAM.md)

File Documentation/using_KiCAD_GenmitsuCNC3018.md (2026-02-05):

-------------------------------------------------------
# KiCAD Tips (for Genmitsu CNC 3018-PRO)

This section provides practical guidelines to reduce common **design and manufacturing issues** when milling PCBs designed in **KiCAD** using the **Genmitsu CNC 3018-PRO** CNC machine
([Amazon link](https://www.amazon.com/Genmitsu-3018-PRO-Control-Engraving-300x180x45mm/dp/B07P6K9BL3)).

<p align="center">
  Genmitsu CNC 3018-PRO
</p>

The **Genmitsu CNC 3018-PRO** is an entry-level, desktop, 3-axis CNC router intended for hobbyists, students, and educational environments. It has a working area of approximately **300 × 180 × 45 mm**, uses a 775 spindle motor, and is controlled via GRBL firmware. The machine is commonly used for engraving and light milling of materials such as wood, plastics, acrylic, **PCB copper boards**, and soft aluminum. While affordable and relatively easy to assemble, it is designed for **prototyping and learning**, not industrial-grade PCB manufacturing.

Although the machine offers reasonable precision, PCB milling imposes strict constraints on **trace width, clearance, and pad size**. Inadequate values can easily result in short circuits, broken traces, or partially milled pads.

## KiCAD Design Guidelines for CNC Milling

Below is an example of a KiCAD PCB layout that follows the recommended guidelines for CNC milling:

<p align="center">
  KiCAD PCB example following CNC milling guidelines
</p>

### Trace Width and Clearance
- Avoid thin traces whenever possible.
- Recommended minimum values for reliable milling:
  - **Trace width:** ≥ **1.0 mm**
    *(Left-click the trace → Properties (E) → Set Track Width to 1 mm)*

  - **Clearance:** ≥ **0.5 mm**
    *(File → Board Setup → Design Rules → Constraints → Minimum Clearance → 0.5 mm)*

- Traces placed too close together may not be fully isolated during milling, leading to **short circuits**.

### Pads and Through-Hole Components
- Through-hole components generally work well on the 3018-PRO, but **pad sizes must be increased**.
- Pads that are too small may be partially removed during isolation milling, resulting in unreliable electrical connections.

- Use **larger rectangular pads** for improved milling results:
  *(Left-click pad → Right-click → Properties (E) → Pad Shape → Rectangular → Size = 2 mm)*

- To apply the same pad settings to all pads:
  1. Right-click the modified pad → **Copy Pad Properties to Default**
  2. Select the remaining pads (**Ctrl + Left-click**)
  3. Right-click → **Paste Default Pad Properties to Selected**

- For **ground planes**, set pad connections to **Solid**:
  *(Left-click pad → Right-click → Properties (E) → Connections → Pad Connection → Solid)*
  This ensures the pad is removed, leaving only the drilled hole.

### Jumpers
- Jumpers can be added directly from the **KiCAD symbol library**.
- The schematic example below shows a jumper implementation:

<p align="center">
  KiCAD schematic jumper example
</p>

- In the PCB layout (`.kicad_pcb`), a jumper can be implemented using a **resistor footprint**.
- To avoid **Design Rule Check (DRC)** errors, connect the resistor pads with a shortcut trace on the **top copper layer (red)**, as shown below:

<p align="center">
  PCB jumper implemented using resistor footprint
</p>

### Board Complexity
- **Single-sided boards** are strongly recommended for use with the Genmitsu CNC 3018-PRO.
- Double-sided boards require precise alignment and are significantly more difficult to mill reliably.

### Final Checks
- Always run **Design Rule Check (DRC)** in KiCAD before exporting fabrication files.

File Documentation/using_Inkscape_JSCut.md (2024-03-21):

# Inkscape & jscut
Each SVG file can be opened in Inkscape to make these files compatible with jscut. This process is brief, and consists of converting all objects present in the SVG into path objects. Select all objects in the graphic area and select the "Path → Object to Path" menu option, followed by the "Path → Stroke to Path" menu option. Exporting this as an SVG with a transparent background is sufficient to progress to jscut. It is helpful to reduce the page size as well. Keybindings make the Inkscape process easy and fast:

"Ctrl + A" - Select all

"Shift + Ctrl + R" - Resize page to selection

"Shift + Ctrl + C" - Object to path conversion

"Ctrl + Alt + C" - Stroke to path conversion

"Ctrl + S" - Save SVG

<p align="center">
  Example SVG Output from Inkscape
</p>

jscut ingests an SVG file and allows configuring various types of toolpaths followed by export to Gcode. Since the PCB milling operation is a single pass at 0.1mm depth-of-cut (and potentially a second operation for pad and via holes), many settings are unused.

* It is recommended to select "Make all mm", set Tool Diameter to 0.1mm, set Pass Depth to 0.1mm, set Rapid to 1000mm/min, and set Plunge and Cut to 100mm/min, before moving on to Operations.

* Select "Open SVG → Local" to open the SVG file exported from Inkscape. If the copper layer graphic does not appear as expected, or appears incomplete or cut off, adjust Inkscape export settings accordingly.

* If all appears as expected, begin selecting path objects in the graphic to create Operations. Multiple Operations can be created per group of objects selected, for example, select all pad and via holes and select "Create Operation", followed by the "Pocket" drop-down option, and a value of "0.1" for the Deep field. The Operation can be expanded to access additional options, such as boolean operations, margin setting, and milling direction.

* After the Pocket Operation, select all copper objects such as pours, pads, vias, and traces (this may take some time with complex designs), then select "Create Operation", followed by the "Outside" drop-down option, and again a value of "0.1" for the Deep field. The Pocket and Outside Operations are sufficient for most designs using through-hole or even surface mount components, but there is potential for more advanced toolpathing as well.

* Select "Simulate GCODE" to verify toolpathing and observe Operation behavior and order.

* Select "Save GCODE" to save the Gcode file.

<p align="center">
  Example Toolpath Output from JScut
</p>

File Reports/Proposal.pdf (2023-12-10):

# Probability Models for Enhancing Calibration of Computer Numerical Control (CNC) Systems

## Jacob Seman, Viktor Woldruff, Tyler Nelson

## Partial Report

## ECEN3810

## Introduction to Probability Theory

ECEN3810 | Jacob Seman, Viktor Woldruff, Tyler Nelson
Introduction to Probability Theory | Fall 2023
Partial Report | Pg. 2

## ~ University of Colorado Boulder ~

## Table of Contents

ECEN3810 | Jacob Seman, Viktor Woldruff, Tyler Nelson
Introduction to Probability Theory | Fall 2023
Partial Report | Pg. 3


## ~ University of Colorado Boulder ~

## I. Executive Summary:

Computer-numerical-control (CNC) printed-circuit-board (PCB) milling is a valuable tool for students in the field of Electrical & Computer Engineering. Milling PCBs requires a well-calibrated CNC mill and a flat PCB surface. Variance exists in the surface of single-sided copper boards, and additional variance is introduced by fixturing methods. This variance must be accounted for, to achieve accurate reproduction of PCB designs, and can be modeled to aid in machine calibration and programmed height offsets, which allows precision machining even when boards are considerably warped by defects or fixturing. Heightmaps of the copper-clad board, where measurements in the Z-axis were taken at regular intervals in the X-Y plane, were produced using the CNC control software

## Candle[1]

, and correlations were identified in the resulting dataset. Normalization was required to remove an observed tilt in the fixturing and expose the subtle variation in the heightmaps. MATLAB was used to generate a variance model showing any observed correlation in X- and Y-axes and compared against the measured data.

## II. Method: Data was collected for the physical system via CNC machine calibration and the resultant

heightmap of 10 single-sided copper-clad boards. This was achieved by the use of the heightmap functionality of the Candle CNC software[2], wherein the software can detect when the metal cutting bit makes electrical contact with the copper-clad board by performing a grid routine of probing contact operations according to user specification[2] [Fig. 1]. All 10 boards were clamped at a specific torque value of 3 NM [Fig. 2], applied to the single fixture clamp bolt using a torque-release hand tool set to this value.

Figure 1 - Candle CNC software performing heightmap operation using electrical contact probing.

Commented [JS1]: The boards themselves don’t have the calibration property, but variation does exist in their surfaces.

ECEN3810 | Jacob Seman, Viktor Woldruff, Tyler Nelson
Introduction to Probability Theory | Fall 2023
Partial Report | Pg. 4


## ~ University of Colorado Boulder ~

Figure 2 - PCB board fixturing specifically designed for 100x70mm PCBs.

## The boards were measured to be 100mm by 70mm, and the heightmap routine was

specified within a 95mm by 65mm region, with a resolution of 34 points by 16 points, in X- and Y-axes, respectively. Once the heightmaps were obtained for all 10 copper boards, a MATLAB script was developed to ingest the heightmap output files and plot a mesh for visual observation [Fig. 3]. Additionally, data was normalized by X and Y linear approximation of the quadrant averages and similarly plotted. This allowed improved visualization of the local variance in Z height, over X and Y, in the resultant surface plots [Fig. 4].

Figure 3 - MATLAB script output showing raw heightmap data.

ECEN3810 | Jacob Seman, Viktor Woldruff, Tyler Nelson
Introduction to Probability Theory | Fall 2023
Partial Report | Pg. 5


## ~ University of Colorado Boulder ~

Figure 4 - MATLAB script output showing normalized heightmap data.

## III. Analysis: A tendency for variance to be higher in the center of the Y-axis was noted, with slight

reduction in variance at the extremes of the X-axis. Conversely, variance was considerably less at the extremes of the Y-axis, with little or no change along the X-axis at these points. This effect is attributable to the fixturing of the PCBs, where the clamping force imparts some flex, typical convex in the Y-axis. A numerical model with adjustable parameters was developed using GeoGebra[3] that allowed replicating this tendency on a 100mm by 70mm 3D surface [Fig. 5].

Figure 5 - GeoGebra numerical surface model with adjustable parameters.

ECEN3810 | Jacob Seman, Viktor Woldruff, Tyler Nelson
Introduction to Probability Theory | Fall 2023
Partial Report | Pg. 6


## ~ University of Colorado Boulder ~

## A matrix of means for the entire dataset was produced by creating a matrix of sums of

variance from the local average for each heightmap and dividing each coordinate sum by the size of the entire dataset. This allowed plotting of a single parabolic surface which represents the mean variance, by coordinate, for the entire dataset of 10 boards. Note that each observed surface imparts some effect on the mean surface. Notably, there is a subtle concavity over the X-axis (with lessened variance just at the X-extremes), and a more dominant convexity over the Y-axis (with a taper toward much lower variance at the Y-extremes) [Fig. 6].

Figure 6 – Normalized mean variance surface, representing the entire dataset across 10 boards.

## Adjusting the numerical model in GeoGebra allows approximation of this ‘saddle’ surface

[Fig. 7]. In reality, this numerical model would benefit from greater order functions in X and Y, to capture the lessened variance at either dimension’s extremes.

Figure 7 - Numerical representation in GeoGebra of mean variance surface.

ECEN3810 | Jacob Seman, Viktor Woldruff, Tyler Nelson
Introduction to Probability Theory | Fall 2023
Partial Report | Pg. 7


## ~ University of Colorado Boulder ~

## Also of note is the consistency of tendencies unique to the X- and Y-axes. A ~10μm ripple

along the X-axis was observed, as well as a sweeping parabola along the Y-axis. Creating vectors of the row and column averages allows plotting in 2D to better observe these features [Fig. 8]. It is suspected that the ripple along the X-axis is induced by the CNC machine itself, likely from a bowed lead screw putting strain on the tool head as it rotates to traverse the gantry along the X-axis. This is likely a common trait among inexpensive desktop CNC machines. Performing a higher resolution heightmap routine would likely reveal that this ripple has a period matching the travel in X per lead screw rotation, which was measured to be roughly 4.3mm. Note that the observed interval is twice this, most likely due to the selected X-resolution of the heightmap coincidentally being near a harmonic of the lead screw rotation interval.

Figure 8 - MATLAB plots of 2D X- and Y-axes mean vectors.

ECEN3810 | Jacob Seman, Viktor Woldruff, Tyler Nelson
Introduction to Probability Theory | Fall 2023
Partial Report | Pg. 8


## ~ University of Colorado Boulder ~

## While the normalized mean dataset provides an excellent visual comparison of local

variations such as the lead-screw effect described above, the raw mean data is most immediately valuable to real-world applications and is a better model of the actual physical PCB when clamped in the fixture [Fig. 9].

Figure 9 – Raw mean variance surface, representing the entire dataset across 10 boards.

Most immediately noticeable is the strong tendency for one side of the fixture to be nearly 0.5mm higher than the other, with few other features represented. This slope is significant and obfuscates any other local variance features observed in the normalized data. While heightmaps created in the Candle software are accurate enough to account for the subtle variation of the lead screw or other local variance in the PCB, the sloped heightmap observed in the raw mean plot may be applied to any PCB clamped in this fixture without the need for creating a heightmap unique to that specific PCB. This is further explored by creating standard deviation plots from the dataset [Fig. 10 & Fig. 11].

Figure 10 – Normalized standard deviation surface, representing the entire dataset across 10 boards.

ECEN3810 | Jacob Seman, Viktor Woldruff, Tyler Nelson
Introduction to Probability Theory | Fall 2023
Partial Report | Pg. 9


## ~ University of Colorado Boulder ~

## The normalized standard deviation surface shows the effect of the quadrant averaging

normalization, which presents itself as near-zero deviation in the center of each quadrant. This method skews the consistency of the fixture clamping surface, causing high deviation at these locations. The raw standard deviation provides more useful information [Fig. 10].

Figure 11 – Raw standard deviation surface, representing the entire dataset across 10 boards.

Standard deviation in the raw data set behaves as expected – with much less deviation at the clamping surfaces. The center of the PCB varies as much as 0.12mm, showing the effect of PCB flexure as the fixture is clamped at consistent torque values. This informs best practices when applying the mean heightmap to an unknown PCB – milling results will be most consistent when fitting smaller designs closer to the lower end of the fixture due to the increased likelihood of the actual PCB position being “on-model” with the mean heightmap. Error percentage was also plotted, wherein each board sample was compared to the mean data [Fig. 12]. This showed areas of higher error per each board. The mean of the error data set is the same as the raw standard deviation, but in terms of percentage error [Fig. 13].

Figure 12 - Percentage error per board, showing areas of greatest deviation from the mean.

ECEN3810 | Jacob Seman, Viktor Woldruff, Tyler Nelson
Introduction to Probability Theory | Fall 2023
Partial Report | Pg. 10


## ~ University of Colorado Boulder ~

Figure 13 – Mean percent error, representing the entire dataset across 10 boards. (Equivalent to std. deviation in percent)

The small size of the data set must be addressed. Only ten boards were acquired for testing, and from a single source, limiting the viability of this model. The most prominent feature of the mean data was noted to be induced by the fixture design, where mean error was as high as 37% [Fig. 13]. “Bootstrapping” of the data set, or resampling via random sampling with replacement, was applied to judge the limit of confidence in the mean data by taking the mean of a larger, generated data set [Fig. 14]. 1000 samples were generated for the bootstrapped data set. Each of these 1000 samples consisted of the mean of 10 random samples from the original data set, chosen with replacement.

Figure 14 – Bootstrapped data set mean. (1000 generated size N sample means)

ECEN3810 | Jacob Seman, Viktor Woldruff, Tyler Nelson
Introduction to Probability Theory | Fall 2023
Partial Report | Pg. 11


## ~ University of Colorado Boulder ~

## The mean of the bootstrap data bears a strong resemblance to the original data set. The

difference between the original mean and the bootstrap mean was also determined. The bootstrap mean was observed to be at most 1.2 microns higher than the original mean in the center of the board, and at most 0.9 microns lower along the upper edge [Fig. 15].

Figure 15 – Difference between bootstrapped data set mean and the original data set mean.

## The standard deviation present in the bootstrapped data was also nearly identical to the

original data set’s standard deviation in terms of relative deviation by coordinate position [Fig. 16]. However, it is important to note that the range of deviation is significantly less than the original data set. The bootstrap scheme imparts this reduction by being significantly larger, and the fact that the overall shape is nearly identical improves confidence in this model. A new map file was generated for use with the Candle CNC software using the bootstrap mean data based on this confidence.

Figure 16 – Standard deviation of bootstrapped data set.

ECEN3810 | Jacob Seman, Viktor Woldruff, Tyler Nelson
Introduction to Probability Theory | Fall 2023
Partial Report | Pg. 12

## ~ University of Colorado Boulder ~

## IV. Results:

In the context of CNC system calibration, the key concepts in probability modeling that are explored are variance and covariance. Variance, as observed in the heightmaps of copper-clad boards, signifies the local deviation in Z-height [Fig. 6]. Meanwhile, covariance, specifically modeled as a parabolic function, highlights the interdependence between variables, emphasizing its significance in understanding the nuanced relationships within the CNC calibration process [Fig. 8].

## Furthermore, while alternative probability models like Markov chains and Monte Carlo

simulation find relevance in various engineering contexts, the specificity of CNC calibration
demands a nuanced approach centered around variance and covariance modeling. Confidence in the resultant mean variance models [Fig. 9 & 14] is supported by the real sample set’s standard deviation [Fig. 11] as well as that of the simulated sample set [Fig. 16].

## Heightmap data was found to show a consistent pattern in variance depending on X and Y

coordinate position. The edges of the board that were in contact with the fixturing typically did not vary as much, but closer to the center of the board a more pronounced variance was observed. This variance was correlated in the X- and Y-axes and became most pronounced in the center of either axis range. The mean represents the expected value of the board height for each X and Y coordinate, and so this was used to generate a model heightmap file which may be tested in the Confluence Hall labs during PCB production.

Lastly, all of the data, scripts, and figures used in this project were compiled into a Github repository[6] for use in the Confluence Hall electronics lab. It is hoped that continued contributions will improve the data set and resultant model to benefit all who use these facilities.

ECEN3810 | Jacob Seman, Viktor Woldruff, Tyler Nelson
Introduction to Probability Theory | Fall 2023
Partial Report | Pg. 13

## ~ University of Colorado Boulder ~

## V. MATLAB Code Appendix Data set, raw and normalized means, raw and normalized standard deviations:

%% Reset
close all;
clear all;
clc;

%% Colormap
map=jet;

%% Plot two figures with east colorbar legend
figure(1)
tiledlayout(2,5);
%meanVal(10)=zeros; not needed due to normalization-this value is ~zero meanPlot(16,34)=zeros;
meanValRaw(10)=zeros;
meanPlotRaw(16,34)=zeros;
stdDevData(16,34,10)=zeros; stdDevDataRaw(16,34,10)=zeros; stdDevPlot(16,34)=zeros;

for i=1:1:10
%% Filename selections
map_num="PCB0"+i+".map";

%% Import *.map file and get mesh parameters for parsing and plotting data=dlmread(map_num,';');
xSize=data(1,3);
ySize=data(1,4);
xRes=data(2,1);
yRes=data(2,2);
xStep=xSize/(xRes-1);
yStep=ySize/(yRes-1);

%% Built plot matrix and parameters plotData=data;
for j=1:3
plotData(1,:)=[];
end
xPlot=0:xStep:xSize;
xMin=min(xPlot,[],'all');
xMax=max(xPlot,[],'all');
xRange=[xMin xMax];
xSteps=(xMax-xMin)/10;
yPlot=0:yStep:ySize;
yMin=min(yPlot,[],'all');
yMax=max(yPlot,[],'all');
yRange=[yMin yMax];
ySteps=(yMax-yMin)/10;

%% Calculate linear approximations from quadrant average and normalize % quadrant averages & linear approximation in x: P1=mean(plotData(1:yRes/2,1:xRes/2),'all'); P2=mean(plotData(1:yRes/2,(xRes/2)+1:xRes),'all'); P3=mean(plotData((yRes/2)+1:yRes,1:xRes/2),'all'); P4=mean(plotData((yRes/2)+1:yRes,(xRes/2)+1:xRes),'all'); Mx_1=(P2-P1)/(xMax/2);
Mx_2=(P4-P3)/(xMax/2);
Mx=(Mx_1+Mx_2)/2; % avg slope in x
% apply normalization in x
for j=1:xRes
for k=1:yRes
plotData(k,j)=plotData(k,j)-Mx*(((j-1)*xStep)-xSize/2); end
end
% quadrant averages & linear approximation in y:

ECEN3810 | Jacob Seman, Viktor Woldruff, Tyler Nelson
Introduction to Probability Theory | Fall 2023
Partial Report | Pg. 14

## ~ University of Colorado Boulder ~

P1=mean(plotData(1:yRes/2,1:xRes/2),'all');
P2=mean(plotData(1:yRes/2,(xRes/2)+1:xRes),'all'); P3=mean(plotData((yRes/2)+1:yRes,1:xRes/2),'all'); P4=mean(plotData((yRes/2)+1:yRes,(xRes/2)+1:xRes),'all'); My_1=(P3-P1)/(yMax/2);
My_2=(P4-P2)/(yMax/2);
My=(My_1+My_2)/2; % avg slope in y
% apply normalization in y
for j=1:xRes
for k=1:yRes
plotData(k,j)=plotData(k,j)-My*(((k-1)*yStep)-ySize/2); end
end
% apply normalization in z
zOffs=mean(plotData,'all');
for j=1:xRes
for k=1:yRes
plotData(k,j)=plotData(k,j)-zOffs; end
end

%% Get normalized mean of whole matrix %meanVal(i)=mean(plotData,'all');
for j=1:xRes
for k=1:yRes
meanPlot(k,j)=meanPlot(k,j)+(plotData(k,j));%-meanVal(i)); stdDevData(k,j,i)=plotData(k,j);%-meanVal(i);
end
end

%% Calculate z-parameters
zMin=min(plotData,[],'all'); zMax=max(plotData,[],'all'); zRange=[zMin zMax];
zSteps=(zMax-zMin)/5;

% first tile
nexttile
s=mesh(xPlot,yPlot,plotData,'FaceAlpha','0.5'); colormap(map);
title('Quadrant Average Normalized 3D Contour '+map_num); xlabel('X-position (mm)')
ylabel('Y-position (mm)')
zlabel('Z-offset (mm)')
xlim(xRange);
xticks(xMin:xSteps:xMax);
ylim(yRange);
yticks(yMin:ySteps:yMax);
zlim(zRange);
zticks(zMin:zSteps:zMax);
s.FaceColor = 'flat';
rotate(s, [0 0 1], 180)
view(325,60);
cb=colorbar('Ticks',zMin:zSteps:zMax); %cb.Layout.Tile='east';
end

figure(2)
tiledlayout(2,5);
for i=1:1:10
%% Filename selections
map_num="PCB0"+i+".map";

%% Import *.map file and get mesh parameters for parsing and plotting data=dlmread(map_num,';');
xSize=data(1,3);
ySize=data(1,4);
xRes=data(2,1);

ECEN3810 | Jacob Seman, Viktor Woldruff, Tyler Nelson
Introduction to Probability Theory | Fall 2023
Partial Report | Pg. 15

## ~ University of Colorado Boulder ~

yRes=data(2,2);
xStep=xSize/(xRes-1);
yStep=ySize/(yRes-1);

%% Plot second map for comparison data=dlmread(map_num,';'); xSize=data(1,3);
ySize=data(1,4);
xRes=data(2,1);
yRes=data(2,2);
xStep=xSize/(xRes-1);
yStep=ySize/(yRes-1);

% Build plot matrix and plot parameters plotData=data;
for j=1:3
plotData(1,:)=[];
end
xPlot=0:xStep:xSize;
xMin=min(xPlot,[],'all');
xMax=max(xPlot,[],'all');
xRange=[xMin xMax];
xSteps=(xMax-xMin)/10;
yPlot=0:yStep:ySize;
yMin=min(yPlot,[],'all');
yMax=max(yPlot,[],'all');
yRange=[yMin yMax];
ySteps=(yMax-yMin)/10;
zMin=min(plotData,[],'all'); zMax=max(plotData,[],'all'); zRange=[zMin zMax];
zSteps=(zMax-zMin)/5;

%% Get raw mean of whole matrix meanValRaw(i)=mean(plotData,'all');
for j=1:xRes
for k=1:yRes
meanPlotRaw(k,j)=meanPlotRaw(k,j)+(plotData(k,j));%-meanValRaw(i)); stdDevDataRaw(k,j,i)=plotData(k,j);%-meanVal(i);
end
end

nexttile
s=mesh(xPlot,yPlot,plotData,'FaceAlpha','0.5'); colormap(map);
title('Raw 3D Contour '+map_num); xlabel('X-position (mm)')
ylabel('Y-position (mm)')
zlabel('Z-offset (mm)')
xlim(xRange);
xticks(xMin:xSteps:xMax);
ylim(yRange);
yticks(yMin:ySteps:yMax);
zlim(zRange);
zticks(zMin:zSteps:zMax);
s.FaceColor = 'flat';
rotate(s, [0 0 1], 180)
view(325,60);
cb=colorbar('Ticks',zMin:zSteps:zMax); %cb.Layout.Tile='east';
end

%% Calculate point means
for j=1:xRes
for k=1:yRes
meanPlot(k,j)=meanPlot(k,j)/10; meanPlotRaw(k,j)=meanPlotRaw(k,j)/10; end

ECEN3810 | Jacob Seman, Viktor Woldruff, Tyler Nelson
Introduction to Probability Theory | Fall 2023
Partial Report | Pg. 16

## ~ University of Colorado Boulder ~

end

%% Plot normalized mean set
% calculate z-parameters
zMin=min(meanPlot,[],'all'); zMax=max(meanPlot,[],'all'); zRange=[zMin zMax];
zSteps=(zMax-zMin)/5;
figure(3)
s=mesh(xPlot,yPlot,meanPlot,'FaceAlpha','0.5');
colormap(map);
title('Normalized Mean Variance (variance from local average across set of 10 heightmaps)'); xlabel('X-position (mm)')
ylabel('Y-position (mm)')
zlabel('Z-variance (mm)')
xlim(xRange);
xticks(xMin:xSteps:xMax);
ylim(yRange);
yticks(yMin:ySteps:yMax);
zlim(zRange);
zticks(zMin:zSteps:zMax);
s.FaceColor = 'flat';
rotate(s, [0 0 1], 180)
view(325,60);
cb=colorbar('Ticks',zMin:zSteps:zMax);

%% Plot raw mean set
% recalculate z-parameters zMin=min(meanPlotRaw,[],'all'); zMax=max(meanPlotRaw,[],'all'); zRange=[zMin zMax];
zSteps=(zMax-zMin)/5;

figure(4)
s=mesh(xPlot,yPlot,meanPlotRaw,'FaceAlpha','0.5');
colormap(map);
title('Raw Mean Variance (variance from local average across set of 10 heightmaps)'); xlabel('X-position (mm)')
ylabel('Y-position (mm)')
zlabel('Z-variance (mm)')
xlim(xRange);
xticks(xMin:xSteps:xMax);
ylim(yRange);
yticks(yMin:ySteps:yMax);
zlim(zRange);
zticks(zMin:zSteps:zMax);
s.FaceColor = 'flat';
rotate(s, [0 0 1], 180)
view(325,60);
cb=colorbar('Ticks',zMin:zSteps:zMax);

%% Plot normalized 2D plot of mean in X and Y meanNVarX=mean(meanPlot,1); meanNVarY=mean(meanPlot,2)';
figure(5)
tiledlayout(2,1)
nexttile
plot(linspace(0,xMax,xRes),meanNVarX) title('Mean Variance Across X'); xlim(xRange);
xticks(xMin:xSteps:xMax);
xlabel('X-position (mm)')
ylabel('Mean Z-Variance (mm)') nexttile
plot(linspace(0,yMax,yRes),meanNVarY) title('Mean Variance Across Y'); xlim(yRange);
xticks(yMin:ySteps:yMax);

ECEN3810 | Jacob Seman, Viktor Woldruff, Tyler Nelson
Introduction to Probability Theory | Fall 2023
Partial Report | Pg. 17

## ~ University of Colorado Boulder ~

xlabel('Y-position (mm)')
ylabel('Mean Z-Variance (mm)')

%% X-Y Std Deviation
% get per-coordinate deviations stdDevPlot=std(stdDevData,0,3); figure(5)
% plot std deviation result
% calculate z-parameters
zMin=min(stdDevPlot,[],'all'); zMax=max(stdDevPlot,[],'all'); zRange=[zMin zMax];
zSteps=(zMax-zMin)/5;

figure(6)
s=mesh(xPlot,yPlot,stdDevPlot,'FaceAlpha','0.5'); colormap(map);
title('Normalized Standard Deviation'); xlabel('X-position (mm)')
ylabel('Y-position (mm)')
zlabel('Std-Dev (mm)')
xlim(xRange);
xticks(xMin:xSteps:xMax);
ylim(yRange);
yticks(yMin:ySteps:yMax);
zlim(zRange);
zticks(zMin:zSteps:zMax);
s.FaceColor = 'flat';
rotate(s, [0 0 1], 180)
view(325,60);
cb=colorbar('Ticks',zMin:zSteps:zMax);

%% Plot Raw Std Deviation
% get per-coordinate deviations stdDevPlotRaw=std(stdDevDataRaw,0,3); figure(7)
% recalculate z-parameters zMin=min(stdDevPlotRaw,[],'all'); zMax=max(stdDevPlotRaw,[],'all');
zRange=[zMin zMax];
zSteps=(zMax-zMin)/5;

s=mesh(xPlot,yPlot,stdDevPlotRaw,'FaceAlpha','0.5'); colormap(map);
title('Raw Standard Deviation');
xlabel('X-position (mm)')
ylabel('Y-position (mm)')
zlabel('Std-Dev (mm)')
xlim(xRange);
xticks(xMin:xSteps:xMax);
ylim(yRange);
yticks(yMin:ySteps:yMax);
zlim(zRange);
zticks(zMin:zSteps:zMax);
s.FaceColor = 'flat';
rotate(s, [0 0 1], 180)
view(325,60);
cb=colorbar('Ticks',zMin:zSteps:zMax);

%% Plot 2D plot of std dev in X and Y stdDevX=mean(stdDevPlot,1); stdDevY=mean(stdDevPlot,2)'; figure(8)
tiledlayout(2,1)
nexttile
plot(linspace(0,xMax,xRes),stdDevX) title('Standard Deviation Across X'); xlim(xRange);

ECEN3810 | Jacob Seman, Viktor Woldruff, Tyler Nelson
Introduction to Probability Theory | Fall 2023
Partial Report | Pg. 18

## ~ University of Colorado Boulder ~

xticks(xMin:xSteps:xMax);
xlabel('X-position (mm)')
ylabel('X-Std-Dev (mm)')
nexttile
plot(linspace(0,yMax,yRes),stdDevY) title('Standard Deviation Across Y'); xlim(yRange);
xticks(yMin:ySteps:yMax);
xlabel('Y-position (mm)')
ylabel('Y-Std-Dev (mm)')

## Published with MATLAB® R2023a (https://www.mathworks.com/products/matlab)

ECEN3810 | Jacob Seman, Viktor Woldruff, Tyler Nelson
Introduction to Probability Theory | Fall 2023
Partial Report | Pg. 19

## ~ University of Colorado Boulder ~

## Fixture re-clamp and difference compare:

%% Reset
close all;
clear all;
clc;

%% Filename selections
map1="PCB07.map";
map2="PCB07b.map";

%% Colormap
map='jet';

%% Import *.map file and get mesh parameters for parsing and plotting data=dlmread(map1,';');
xSize=data(1,3);
ySize=data(1,4);
xRes=data(2,1);
yRes=data(2,2);
xStep=xSize/(xRes-1);
yStep=ySize/(yRes-1);

%% Build plot matrix and plot parameters plotData1=data;
for i=1:3
plotData1(1,:)=[];
end
xPlot=0:xStep:xSize;
xMin=min(xPlot,[],'all');
xMax=max(xPlot,[],'all');
xRange=[xMin xMax];
xSteps=(xMax-xMin)/10;
yPlot=0:yStep:ySize;
yMin=min(yPlot,[],'all');
yMax=max(yPlot,[],'all');
yRange=[yMin yMax];
ySteps=(yMax-yMin)/10;
zMin=min(plotData1,[],'all'); zMax=max(plotData1,[],'all');
zRange=[zMin zMax];
zSteps=(zMax-zMin)/10;

%% Plot two figures with east colorbar legend tiledlayout(2,2);
% first figure
nexttile
s=mesh(xPlot,yPlot,plotData1,'FaceAlpha','0.5'); colormap(map);
title('3D Contour '+map1);
xlim(xRange);
xticks(xMin:xSteps:xMax);
ylim(yRange);
yticks(yMin:ySteps:yMax);
zlim(zRange);
zticks(zMin:zSteps:zMax);
s.FaceColor = 'flat';
rotate(s, [0 0 1], 180)
view(325,60);
cb=colorbar('Ticks',zMin:zSteps:zMax); cb.Layout.Tile='east';
% second figure
nexttile
s=mesh(xPlot,yPlot,plotData1,'FaceAlpha','0.5'); title('2D Contour '+map1);
xlim(xRange);
xticks(xMin:xSteps:xMax);
ylim(yRange);

ECEN3810 | Jacob Seman, Viktor Woldruff, Tyler Nelson
Introduction to Probability Theory | Fall 2023
Partial Report | Pg. 20

## ~ University of Colorado Boulder ~

yticks(yMin:ySteps:yMax);
zlim(zRange);
s.FaceColor = 'flat';
rotate(s, [0 0 1], 180)
view(2);
clim(zRange);

%% Plot second map for comparison data=dlmread(map2,';');
xSize=data(1,3);
ySize=data(1,4);
xRes=data(2,1);
yRes=data(2,2);
xStep=xSize/(xRes-1);
yStep=ySize/(yRes-1);

% Build plot matrix and plot parameters plotData2=data;
for i=1:3
plotData2(1,:)=[];
end
xPlot=0:xStep:xSize;
xMin=min(xPlot,[],'all');
xMax=max(xPlot,[],'all');
xRange=[xMin xMax];
xSteps=(xMax-xMin)/10;
yPlot=0:yStep:ySize;
yMin=min(yPlot,[],'all');
yMax=max(yPlot,[],'all');
yRange=[yMin yMax];
ySteps=(yMax-yMin)/10;
zMin=min(plotData2,[],'all'); zMax=max(plotData2,[],'all'); zRange=[zMin zMax];
zSteps=(zMax-zMin)/10;

% first figure
nexttile
s=mesh(xPlot,yPlot,plotData2,'FaceAlpha','0.5'); colormap(map);
title('3D Contour '+map2);
xlim(xRange);
xticks(xMin:xSteps:xMax);
ylim(yRange);
yticks(yMin:ySteps:yMax);
zlim(zRange);
zticks(zMin:zSteps:zMax);
s.FaceColor = 'flat';
rotate(s, [0 0 1], 180)
view(325,60);
cb=colorbar('Ticks',zMin:zSteps:zMax); cb.Layout.Tile='east';
% second figure
nexttile
s=mesh(xPlot,yPlot,plotData2,'FaceAlpha','0.5'); title('2D Contour '+map2);
xlim(xRange);
xticks(xMin:xSteps:xMax);
ylim(yRange);
yticks(yMin:ySteps:yMax);
zlim(zRange);
s.FaceColor = 'flat';
rotate(s, [0 0 1], 180)
view(2);
clim(zRange);

%% compare board differences figure(2)

ECEN3810 | Jacob Seman, Viktor Woldruff, Tyler Nelson
Introduction to Probability Theory | Fall 2023
Partial Report | Pg. 21

## ~ University of Colorado Boulder ~

tiledlayout(1,2)
nexttile
diffData(yRes,xRes,2)=zeros; diffData(:,:,1)=plotData1; diffData(:,:,2)=plotData2; diffData=std(diffData,0,3); zMin=min(diffData,[],'all'); zMax=max(diffData,[],'all');
zRange=[zMin zMax];
zSteps=(zMax-zMin)/10;
s=mesh(xPlot,yPlot,diffData,'FaceAlpha','0.5'); colormap(map);
title('3D Difference Contour - Remove and Reclamp'); xlim(xRange);
xticks(xMin:xSteps:xMax);
ylim(yRange);
yticks(yMin:ySteps:yMax);
zlim(zRange);
zticks(zMin:zSteps:zMax);
s.FaceColor = 'flat';
rotate(s, [0 0 1], 180)
view(325,60);
cb=colorbar('Ticks',zMin:zSteps:zMax); cb.Layout.Tile='east';
nexttile
s=mesh(xPlot,yPlot,diffData,'FaceAlpha','0.5'); title('2D Difference Contour - Remove and Reclamp'); xlim(xRange);
xticks(xMin:xSteps:xMax);
ylim(yRange);
yticks(yMin:ySteps:yMax);
zlim(zRange);
s.FaceColor = 'flat';
rotate(s, [0 0 1], 180)
view(2);
clim(zRange);

## Published with MATLAB® R2023a (https://www.mathworks.com/products/matlab)

ECEN3810 | Jacob Seman, Viktor Woldruff, Tyler Nelson
Introduction to Probability Theory | Fall 2023
Partial Report | Pg. 22

## ~ University of Colorado Boulder ~

## Bootstrap data generation and heightmap model file generation:

%% Reset
close all;
clear all;
clc;

%% Colormap
colormap(jet);

%% Init data and parameters
% Import *.map file and get mesh parameters for parsing and plotting data(:,:)=dlmread("PCB01.map",';');
xSize=data(1,3);
ySize=data(1,4);
xRes=data(2,1);
yRes=data(2,2);
xStep=xSize/(xRes-1);
yStep=ySize/(yRes-1);
xPlot=0:xStep:xSize;
xMin=min(xPlot,[],'all');
xMax=max(xPlot,[],'all');
xRange=[xMin xMax];
xSteps=(xMax-xMin)/10;
yPlot=0:yStep:ySize;
yMin=min(yPlot,[],'all');
yMax=max(yPlot,[],'all');
yRange=[yMin yMax];
ySteps=(yMax-yMin)/10;
data(19,34)=zeros;
for i=1:1:10
% Filename selections
map_num="PCB0"+i+".map";
% Import *.map file and get mesh parameters for parsing and plotting data(:,:,i)=dlmread(map_num,';');
end
% Correct matrix
for j=1:1:3
data(1,:,:)=[];
end

%% Per-coordinate means
meanData=mean(data,3);
figure(1)
% recalculate z-parameters zMin=min(meanData,[],'all'); zMax=max(meanData,[],'all');
zRange=[zMin zMax];
zSteps=(zMax-zMin)/5;
s=mesh(xPlot,yPlot,meanData,'FaceAlpha','0.5');
title('Raw Mean Variance (variance from local average across set of 10 heightmaps)'); xlabel('X-position (mm)')
ylabel('Y-position (mm)')
zlabel('Z-variance (mm)')
xlim(xRange);
xticks(xMin:xSteps:xMax);
ylim(yRange);
yticks(yMin:ySteps:yMax);
zlim(zRange);
zticks(zMin:zSteps:zMax);
s.FaceColor = 'flat';
rotate(s, [0 0 1], 180)
view(325,60);
cb=colorbar('Ticks',zMin:zSteps:zMax);

%% Per-board %-error from mean figure(2)
errorBoard(16,34,10)=zeros;

ECEN3810 | Jacob Seman, Viktor Woldruff, Tyler Nelson
Introduction to Probability Theory | Fall 2023
Partial Report | Pg. 23

## ~ University of Colorado Boulder ~

colormap(jet);
tiledlayout(2,5)
for i=1:1:10
nexttile
errorBoard(:,:,i)=(abs(data(:,:,i)-meanData)./mean(meanData,'all')).*100; % recalculate z-parameters
zMin=min(errorBoard(:,:,i),[],'all'); zMax=max(errorBoard(:,:,i),[],'all');
zRange=[zMin zMax];
zSteps=(zMax-zMin)/5;
s=mesh(xPlot,yPlot,errorBoard(:,:,i),'FaceAlpha','0.5'); title("Percentage Error From Mean - PCB #"+i); xlabel('X-position (mm)')
ylabel('Y-position (mm)')
zlabel('Error (%)')
xlim(xRange);
xticks(xMin:xSteps:xMax);
ylim(yRange);
yticks(yMin:ySteps:yMax);
zlim(zRange);
zticks(zMin:zSteps:zMax);
s.FaceColor = 'flat';
rotate(s, [0 0 1], 180)
view(325,60);
cb=colorbar('Ticks',zMin:zSteps:zMax);
end

%% Mean percent error, note: this is the same as standard deviation figure(3)
meanError=mean(errorBoard,3);
colormap(jet);
% recalculate z-parameters zMin=min(meanError,[],'all'); zMax=max(meanError,[],'all');
zRange=[zMin zMax];
zSteps=(zMax-zMin)/5;
s=mesh(xPlot,yPlot,meanError,'FaceAlpha','0.5');
title('Mean Percent Error (variance from local average across set of 10 heightmaps)'); xlabel('X-position (mm)')
ylabel('Y-position (mm)')
zlabel('Error (%)')
xlim(xRange);
xticks(xMin:xSteps:xMax);
ylim(yRange);
yticks(yMin:ySteps:yMax);
zlim(zRange);
zticks(zMin:zSteps:zMax);
s.FaceColor = 'flat';
rotate(s, [0 0 1], 180)
view(325,60);
cb=colorbar('Ticks',zMin:zSteps:zMax);

%% Create additional samples using bootstrap method bootData(16,34,1000)=zeros;
for i=1:1:1000
for j=1:1:10
% sample randomly from real dataset, sum bootData(:,:,i)=bootData(:,:,i)+data(:,:,randi([1 10])); end
bootData(:,:,i)=bootData(:,:,i)/10;
end

%% Plot the mean of the bootstrap data figure(4)
meanBoot=mean(bootData,3); colormap(jet);
% recalculate z-parameters zMin=min(meanBoot,[],'all');

ECEN3810 | Jacob Seman, Viktor Woldruff, Tyler Nelson
Introduction to Probability Theory | Fall 2023
Partial Report | Pg. 24

## ~ University of Colorado Boulder ~

zMax=max(meanBoot,[],'all');
zRange=[zMin zMax];
zSteps=(zMax-zMin)/5;
s=mesh(xPlot,yPlot,meanBoot,'FaceAlpha','0.5');
title('Bootstrap Mean Variance (from bootstrap data with 1000 generated size=N samples)'); xlabel('X-position (mm)')
ylabel('Y-position (mm)')
zlabel('Z-variance (mm)')
xlim(xRange);
xticks(xMin:xSteps:xMax);
ylim(yRange);
yticks(yMin:ySteps:yMax);
zlim(zRange);
zticks(zMin:zSteps:zMax);
s.FaceColor = 'flat';
rotate(s, [0 0 1], 180)
view(325,60);
cb=colorbar('Ticks',zMin:zSteps:zMax);

%% Plot the std dev of the bootstrap data figure(5)
stdDevBoot=std(bootData,0,3); colormap(jet);
% recalculate z-parameters zMin=min(stdDevBoot,[],'all'); zMax=max(stdDevBoot,[],'all');
zRange=[zMin zMax];
zSteps=(zMax-zMin)/5;
s=mesh(xPlot,yPlot,stdDevBoot,'FaceAlpha','0.5');
title('Bootstrap Standard Deviation (from bootstrap data with 1000 generated size=N samples)');
xlabel('X-position (mm)')
ylabel('Y-position (mm)')
zlabel('Z-variance (mm)')
xlim(xRange);
xticks(xMin:xSteps:xMax);
ylim(yRange);
yticks(yMin:ySteps:yMax);
zlim(zRange);
zticks(zMin:zSteps:zMax);
s.FaceColor = 'flat';
rotate(s, [0 0 1], 180)
view(325,60);
cb=colorbar('Ticks',zMin:zSteps:zMax);

%% Different between meanData and meanBoot figure(6)
diffBoot=meanBoot-meanData; colormap(jet);
% recalculate z-parameters zMin=min(diffBoot,[],'all'); zMax=max(diffBoot,[],'all');
zRange=[zMin zMax];
zSteps=(zMax-zMin)/5;
s=mesh(xPlot,yPlot,diffBoot,'FaceAlpha','0.5'); title("Difference between meanData and meanBoot"); xlabel('X-position (mm)')
ylabel('Y-position (mm)')
zlabel('Z-variance (mm)')
xlim(xRange);
xticks(xMin:xSteps:xMax);
ylim(yRange);
yticks(yMin:ySteps:yMax);
zlim(zRange);
zticks(zMin:zSteps:zMax);
s.FaceColor = 'flat';
rotate(s, [0 0 1], 180)
view(325,60);

ECEN3810 | Jacob Seman, Viktor Woldruff, Tyler Nelson
Introduction to Probability Theory | Fall 2023
Partial Report | Pg. 25

## ~ University of Colorado Boulder ~

cb=colorbar('Ticks',zMin:zSteps:zMax);

%% Write out bootstrap model
% get map parameters from another map bootModel=dlmread("PCB01.map",';'); for i=1:1:16
for j=1:1:34
bootModel(i+3,j)=bootData(i,j); end
end
% write to file using ';' delimiter
% header:
fid=fopen('bootModel.map','w'); % filename, write mode fprintf(fid,"%d;%d;%d;%d\n",bootModel(1,1),bootModel(1,2),bootModel(1,3),bootModel(1,4)); fprintf(fid,"%d;%d;%.2f;%.2f\n",bootModel(2,1),bootModel(2,2),bootModel(2,3),bootModel(2,4)); fprintf(fid,"%d;%d;%d\n",bootModel(3,1),bootModel(3,2),bootModel(3,3));
% data:
for i=4:1:19
for j=1:1:33
fprintf(fid,"%.16f;",bootModel(i,j)); end
fprintf(fid,"%.16f\n",bootModel(i,34)); end
fclose(fid);

## Published with MATLAB® R2023a (https://www.mathworks.com/products/matlab)

## VI. References:

1. Denvi. (n.d.). Denvi/Candle: GRBL controller application with G-code visualizer written in Qt.

## GitHub. https://github.com/Denvi/Candle

2. George. (2023, March 10). How to utilize height mapping in candle. SainSmart Resource Center.

## https://docs.sainsmart.com/article/kj4xzak19j-how-to-utilize-height-mapping-in-candle

3. Seman, Jacob. “PCB Mesh Model - 3D Calculator.” GeoGebra, www.geogebra.org/3d/gc2grpqr. Accessed 4 Dec. 2023.
4. Claudet, A., Tran, H., & Su, J.-C. (2008). Quantification of uncertainty in machining operations for on-machine acceptance. Office of Scientific and Technical Information (OSTI).

## https://doi.org/10.2172/945903

5. Ignacio Lira, George Cargill. Uncertainty analysis of positional deviations of CNC machine tools, Precision Engineering, Volume 28, Issue 2, 2004, Pages 232-239, ISSN 0141-6359,

## https://doi.org/10.1016/j.precisioneng.2003.06.001

6. Seman, Jacob, PCB_MFG, (2023), GitHub repository,

## https://github.com/Jbsco/PCB_MFG/reports/

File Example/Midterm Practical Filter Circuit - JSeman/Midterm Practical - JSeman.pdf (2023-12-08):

### Variable Active Filter Designs

Jacob Seman

Midterm Practical Design

EECE226L-001, Spring 2023

Dr. Mellenthin

### Contents:

EECE226L | Jacob Seman
Circuits as Systems Design Lab | Spring 2023
Practical Design Midterm | Page 3

Background:

The goal of this report is to test and quantify characteristics of some of the more notable op-amps widely used in the audio industry. Active filters present a unique opportunity – they may be designed for any gain behavior across the frequency spectrum – a variable design is even better. Specifically, the filter should provide consistent, narrow bandwidth amplification, and be adjustable across the audible frequencies occupied by typical synthesizers; roughly 50Hz through 4200Hz, though the entire audible spectrum would be a plus. Such a filter might be able to be used in conjunction with a noise generator for the input, and some gain normalization on the output.

A filter with an adjustable center frequency seems ideal. The Sallen-Key topology is able to support setting the Q without affecting the center frequency. Although Q and the gain at the center frequency cannot be changed independently, band-pass designs allow varying the center frequency with a single resistor. A design such as this would allow building two such filters into a single “dual” op-amp package, while varying both center frequency resistors with a single 2-gang potentiometer. This would comprise a stereo filter with identical performance and characteristics for both channels and could take advantage of some of the higher-end audio op-amps’ crosstalk rejection capability. A state-variable filter topology, such as the Kerwin–Huelsman–Newcomb design, would be another design worth investigating, as Q can be precisely set and controlled while the center frequency may be varied independently, although gain is again linked to Q. These designs sum a signal with its integral and double-integral, and being biquad designs, require multiple op-amps to build, but are more tolerant of lower-performance ICs. A stereo filter design using this topology would require 3 dual op-amps and a 4-gang potentiometer. The integrator op-amps may be replaced with control voltage sources, as is usually the case with modular synthesizers – this would be a desirable option to pursue at a later date. Regardless, as the filters would need to sweep the desired range and provide consistent gain, testing a handful of op-amps for consistent center frequency gain across the sweep seems like a good first step.

Op-amps on-hand to be tested and/or simulated include:

Texas Instruments: | LM833N
| LM4562NA
| LME49720NA (die identical to 4562)
Japan Radio Company: | NJM/JRC4556AD
| NJM/JRC4580D
Burr-Brown: | OPA2132P
| OPA2277P

Practical Design Midterm | Page 4

Design Specifications:

High-Q, (30 to 50, option to adjust with potentiometer a plus)

High gain, (+20 to +40 dB, option to adjust with potentiometer a plus, linked to Q acceptable)

Variable center frequency (80Hz through 4200Hz, 50Hz through 20kHz a plus)

Consistent Q and gain across variable frequency (less than +/- 5 dB variation from min. to max.)

Preliminary Testing:

Op-amps are known to vary in performance and may not be able to maintain consistent output across these frequencies. A testing scheme was devised wherein each op-amp was simulated in a unity-gain low-pass Sallen-Key filter circuit [1, fig. 3.23] with a high-Q setting and low center frequency. The filter characteristics can be calculated and compared against the simulation result to make a determination of the op-amps’ performance. If an op-amp should fall short of the expected response, or if the center frequency varies significantly, then the op-amp may be unsuitable for the design specifications. If any should perform better than the rest by a wide margin, then they would likely be best suited for building the practical circuit.


Figure 1: Simulation test circuit. Sallen-Key low-pass with low-frequency, high-Q setting.

Practical Design Midterm | Page 5

Here, K = 1, and R1 = R2 = R. To achieve a high Q setting from on-hand values, C1 and C2 are set quite disparately. For a low-pass Sallen-Key, the center frequency is given by:

ω0 = (√R1C1R2C2)

−1
→ ω0 = (R√C1C2)

−1

ω0 = (1M√(0.1μ)(10p))

−1
= 1000 rad/s = 159.155 Hz

Q is given by:

Q = ((1 − K)√R1C1/R2C2 + √R1C2/R2C1 + √R2C2/R1C1)

−1
→ Q = (2√C2/C1)

−1

Q = (2√(0.1μ)(10p))

−1
= 50

And the transfer function itself is given by:

Vo
Vi

(jω) =

K
(R1C1R2C2
(jω)

2 + jω((1 − K)R1C1 + R1C2 + R2C2) + 1)

Vo
Vi

(jω) = (R

2C1C2
(jω)

2 + jω(2RC2
) + 1)

−1

Vo
Vi

(j1000) = ((1M)

2
(0.1μ)(10p)(j1000)

2 + j1000(2(1M)(10p)) + 1)

−1
| = (50∠ − 90°) V/V

For a gain (in dB) of:

20 log(50) = 33.979 dB

We should expect to see a center frequency response near 159.155 Hz, Q approaching 50, and magnitude approaching 33.979 dB.

Spice directives were applied to directly find measurements of interest for each op-amp simulated. Namely: center frequency, bandwidth, Q, and magnitude. The circuit was duplicated in LTSpice to allow plotting and measuring of all op-amps in the same simulation, providing a visual comparison of responses. The results of this simulation are presented below, and on the next page.

Op-Amp | f0 (Hz) | BW (Hz) | Q (f/BW) | Vo/Vi | dB
LM833 | 159.074 | 3.34386 | 47.5721 | 47.5887 | 33.5501
LM4562 | 157.543 | 3.22595 | 48.8362 | 48.8509 | 33.7774
NJM4556 | 158.782 | 8.03165 | 19.7695 | 19.7885 | 25.9282
NJM4580 | 158.855 | 10.7173 | 14.8223 | 14.8482 | 23.4335
OPA2132 | 159.001 | 3.31353 | 47.9854 | 48.0165 | 33.6278
OPA2277 | 138.420 | 3.19061 | 43.3837 | 43.4074 | 32.7513

[1, eqn. 3.60b]

[1, eqn. 3.60c]

[1, pg. 143]


Circuits as Systems Design Lab | Spring 2023
Practical Design Midterm | Page 6

Figure 2: LTSpice bode plot of op-amps under test, showing low-pass high-Q characteristics, with variation in center frequency, Q, peak magnitude, and phase.


Circuits as Systems Design Lab | Spring 2023
Practical Design Midterm | Page 7

Figure 3: The same simulation plot, with attention to the peak response at the calculated center frequency. [Note: LM833 obscured by nearly identical OPA2132 trace]

Practical Design Midterm | Page 8

Low frequency, high-Q circuits appear to present a challenge for op-amps. It is clear that NJM4556 and NJM4580 are not capable of meeting the Q specification, reaching only 19.7695 and 14.8223 respectively, although they were able to produce an accurate center frequency peak response. Also note OPA2277’s unusual 138.420Hz peak response. The same circuit was tested with R = 6.8 kΩ to observe high frequency performance, however all op-amps had little issue achieving Q ≅ 50, although OPA2277 and NJM4556 both showed lower center frequency peak responses. This seems reason enough to strongly consider the remaining LM833, LM4562/LME49720, and OPA2132 op-amps for continued testing, but perhaps a detailed comparison of the high frequency results will show a singular best-in-class selection.

For R = 6.8 kΩ, the expected results are:

ω0 = (6.8k√(0.1μ)(10p))

−1
= 147.059 krad/s = 23.405 kHz

Q = (2√(0.1μ)(10p))

−1
= 50

Vo
Vi

(j147.059k) = ((6.8k)

2
(0.1μ)(10p)(j147.059k)

2 + j147.059k(2(6.8k)(10p)) + 1)

| −1

Vo
Vi

(j147.059k) = (50∠ − 90°) V/V

For a gain (in dB) of:

20 log(50) = 33.979 dB

We should expect to see a center frequency response near 23.405 kHz, Q approaching 50, and magnitude approaching 33.979 dB. The results are again presented below and on the next page, and show LM4562 as nearest to the majority of calculated values. LM4562/LME49720 will be selected for continued design and built circuits.

Op-Amp | f0 (kHz) | BW (Hz) | Q (f/BW) | Vo/Vi | dB
LM833 | 21.518 | 414.146 | 51.9573 | 51.9658 | 34.3144
LM4562 | 22.699 | 447.797 | 50.6896 | 50.7114 | 34.1021
NJM4556 | 19.934 | 400.240 | 49.8057 | 49.7801 | 33.9411
NJM4580 | 21.787 | 426.795 | 51.0483 | 51.0138 | 34.1538
OPA2132 | 21.301 | 401.064 | 53.1112 | 53.1073 | 34.5031
OPA2277 | 18.450 | 346.409 | 53.2611 | 53.2733 | 34.5302


Circuits as Systems Design Lab | Spring 2023
Practical Design Midterm | Page 9

Figure 4: High frequency simulation plot with attention to peak response, showing LM4562/LME49720 nearest to the calculated center frequency of 23.405 kHz.

Practical Design Midterm | Page 10

Design:

The low-pass Sallen-Key circuit was acceptable for testing op-amps, but was unable to meet the design specifications without resorting to a very large range on the input resistor network, making it more difficult to implement as adjustable with high Q, when using a dual-gang potentiometer. Band-pass variations were attempted, but varying frequency proved unwieldy and again required a wide range of resistor network values. Some improvement was found with a multiple-feedback design, however the resistor network required vastly different values, out of proportion to one-another, to adjust the center frequency without affecting all other characteristics, rendering it difficult to implement with any kind of multi-gang potentiometer. Ultimately, a simplified state-variable Kerwin–Huelsman–Newcomb filter [2][3] was found to provide the specified characteristics, similar to the multiple-feedback design, while being able to be controlled with a dual-gang potentiometer per channel. The multiple integrator topology allowed for discrete variation of filter characteristics, which afforded rapid progress in achieving specifications.


Figure 5: Simulation design circuit. Simplified state-variable filter.

Note that the first stage, U1, is a summing amplifier with the outputs from the second stage integrator, U2, and Vin as non-inverting inputs, and the output from the third stage integrator, U3, as an inverting input. Essentially, U1 sums Vin with the band-pass response from U2, and subtracts the low-pass response from U3. The two integrators may be designed with the same time constant, which provides a single center frequency rather than two corners – this comprises the band-pass characteristic by integrating the high-pass response of the summed signals.

This also means that each integrator stage has its corner frequency set independently from the rest of the circuit. If they are set the same as each other, where C1 = C2 = C and Rfc1 = Rfc2 = Rfc

, then
the circuit’s center frequency can be determined. This means that the state-variable filter has the same formula for center frequency as an integrator filter’s corner frequency:

ωc = (Rfc

C)

−1
[3, img. 4]

Practical Design Midterm | Page 11

Consider the audible frequency range of 50Hz to 20kHz, and say C = 0.1 μF:

ωc1 = 2π50 = 314.159 rad/s

ωc2 = 2π20k = 125.664 rad/s

The range of Rfc

needed for this filter can be determined:

ωc = (Rfc

C)

−1
→ Rfc = (ωcC)

−1

Rfc1 = ((314.159)(0.1u))

−1
= 31830.99 Ω

Rfc2 = ((125.664k)(0.1u))

−1
= 79.577 Ω

Already this is an improvement over the Sallen-Key filter, as the resistance values required for the entire audible spectrum are much lower. Consider the narrower range, occupied by synthesizer instruments, 80Hz through 4200Hz:

Rfc1 = ((502.655)(0.1u))

−1
= 19894.37 Ω

Rfc2 = ((26389.378)(0.1u))

−1
= 378.94 Ω

4-gang potentiometers with a range up to 20 kΩ are available, so this design seems worth pursuing with C = 0.1 μF, but perhaps it can be improved. Selecting C = 0.33 μF may work out even more conveniently:

Rfc1 = ((314.159)(0.33u))

−1
= 9645.76 Ω

Rfc2 = ((125.664k)(0.33u))

−1
= 24.11 Ω

This allows varying from 50Hz through 20kHz with a 10kΩ potentiometer, which are inexpensive and commonly available with good precision in a variety of different packages and tapers, including linear and audio tapers.

The Q-factor is related to the damping coefficient as:

2ξ = Q

−1

Where 2ξ is represented by the resistor network as:

2ξ =

1
Q

=

R1

(R3 + R4

)
R4

(R1 + R2

)

√
R3
R4

And set the two feedback resistors R3 = R4 = R3.4:

1
Q

=

R12R3.4

R3.4

(R1 + R2

)

→

1
Q

=

R1R3.4
R1 + R2

[3, img. 21]

Practical Design Midterm | Page 12

If R3.4 is set to R3.4 = 10 kΩ:

1
Q

= 2

R1
R1 + R2

→ Q =

R1 + R2
2R1

In terms of the individual R values:

R2 = R1

(2Q − 1)

R1 = R2/(2Q − 1)

If we set Q = 40, the middle of the specified range:

R2 = R1

(2(40) − 1) → R2 = R179

R1 = R2/(2(40) − 1) → R1 = R2/79

Now these values can be set for the required Q based on available resistor values. If R1 = 130 Ω, available in the E24 5% and 1% tolerance preferred value group, then R2 = 10270 Ω ≅ 10 kΩ.


Figure 6: Simplified state-variable filter with values determined to meet design specifications.

The transfer function for the state-variable filter’s DC passband gain is given by:

A0 =

1
RC ∙

R2

(R3 + R4

)
R3

(R1 + R2

)
R3
R4RC +

1
ωRC (

R1

(R3 + R4

)
R4

(R1 + R2

)

) +

1
ωRC

A0 =

ωR2R4

(R3 + R4

)
R3

(ωR3

(R1 + R2

) + R4

(2R1 + R2

) + R1R3

)

A0 =

2ωR2R3.4

2

R3.4

2
(ω(R1 + R2

) + 3R1 + R2

)

[3, img. 15]

Practical Design Midterm | Page 13

For peak magnitude at ω, multiply by the Q:

Vout

Vin

(ω) =

2ωQR2R3.4

2

R3.4

2
(ω(R1 + R2

) + 3R1 + R2

)

Simulation Results:

For the initial simulation, set RcFset = 482 Ω for a peak response at:

ωc = ((482)(0.33u))

−1 = 6286.94 rad/s = 1000.60 Hz

Q has been set by R1 and R2:

Q =

(130) + (10k)
2(130)

= 38.96

And the expected DC passband gain at ω = 6286.94 rad/s:

Vout

Vin

(ω) =

2(6286.94)(38.96)(10k)(10k)

2

(10k)

2 ((6286.94)((130) + (10k)) + 3(130) + (10k))

= 76.9075 V/V

For a gain (in dB) of:

20 log(76.907) = 37.7194 dB

Several other center frequencies were calculated for comparison against the simulation:

RcFset (Ω) | f0 (Hz) | Q (f/BW) | Vo/Vi | dB
24.11 | 20003.6378 | 38.96 | 76.9194 | 37.7207
48.2 | 10005.9690 | 38.96 | 76.9188 | 37.7206
482 | 1000.5969 | 38.96 | 76.9075 | 37.7457
4820 | 100.0597 | 38.96 | 76.7948 | 37.7066
9645.76 | 49.9999 | 38.96 | 76.6697 | 37.6925

The results of the simulations are presented below, and on the next page.

RcFset (Ω) | f0 (Hz) | BW (Hz) | Q (f/BW) | Vo/Vi | dB
24.11 | 19998.6 | 476.775 | 41.9456 | 82.8245 | 38.3632
48.2 | 10004.6 | 248.572 | 40.2483 | 79.4660 | 38.0036
482 | 1000.46 | 25.6111 | 39.0636 | 77.1408 | 37.7457
4820 | 100.046 | 2.56789 | 38.9604 | 76.9401 | 37.7231
9645.76 | 50.0035 | 1.28323 | 38.9669 | 76.9322 | 37.7222


Circuits as Systems Design Lab | Spring 2023
Practical Design Midterm | Page 14

Figure 7: Bode plot of state-variable filter at various settings, showing band-pass high-Q characteristics, with variation in center frequency.

Practical Design Midterm | Page 15

Conclusion:

The simplified state-variable topology was observed to meet the design specifications and could likely exceed them as needed when high quality op-amps are used. The center frequency was able to be varied, and could be controlled using a dual-gang 10kΩ potentiometer. The formula for Q was also shown to be dependent on R1 and R2, and so could easily be varied across a range using a single potentiometer as well. The peak response and Q was consistent across the frequency range tested, with minor variance. The design would be easy to build using the op-amps tested, and uses readily available components. Extensibility of the state-variable topology is also quite good, as the integrator stages can be replaced by control voltages to automate or otherwise selectively control the filter’s characteristics.

The practical lab portion of this experiment should include building the circuit with measured component values and creating a table of actual response measurements under conditions and settings as near to the simulated cases as possible. Using the actual component values, recalculate the expected results using the formulas in this report, and compare against the measured responses. If possible, connect the filter to an audio source and an output to observe the filters effects. If necessary, create a passive attenuator resistor network to adjust the source to a decibel level appropriate for the expected actual filter response. Likewise, apply an output buffer to the output if needed. Does the filter behave as expected? Make a statement on the performance of the filter and suggest improvements or adjustments. If time permits, consider building the filter circuit using DIP-8 sockets, and switch out the LM4562 for other op-amps. Take brief measurements on the oscilloscope and listen to the audio source again, and make a subjective statement on whether the differences are audible.

Practical Design Midterm | Page 16

References:

[1] S. Franco, Design with Operation Amplifiers and Analog Integrated Circuits, 4th Ed. McGraw Hill, 2015.
[2] A. M. Soliman and A. H. Madian, “MOS-C KHN Filter Using Voltage Op Amp, CFOA, OTRA and DCVC,” Journal of Circuits, Systems, and Computers, Vol. 18, No. 4 733–769, 2009.
[3] “State Variable Filter,” Electronics Tutorials [website] Available: Electronics Tutorials, https://www.electronics-tutorials.ws/filter/state-variable-filter.html

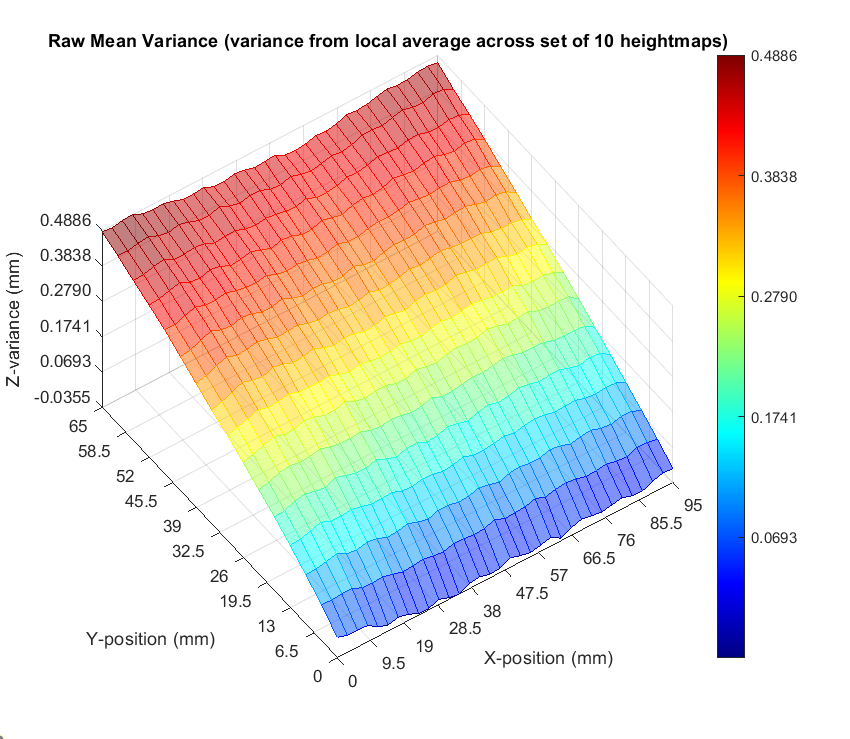
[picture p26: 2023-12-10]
Reports/raw_mean.png

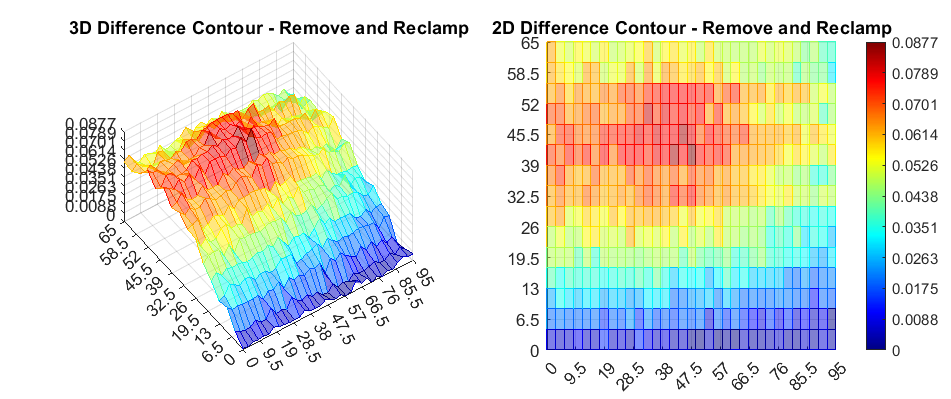
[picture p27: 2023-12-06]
Reports/reclamp std dev 07.png

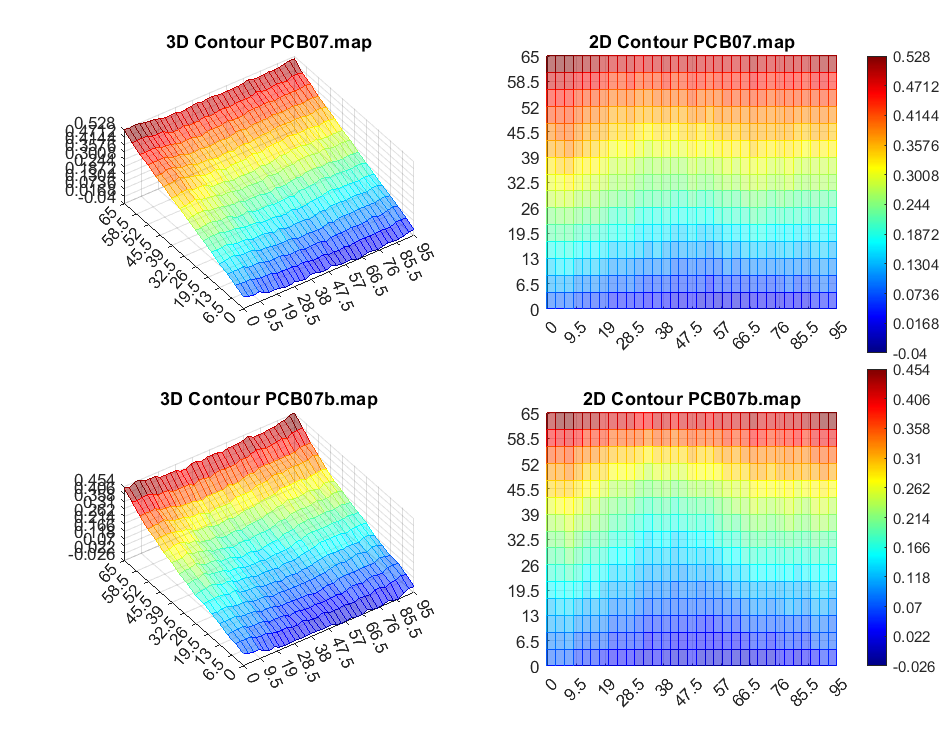
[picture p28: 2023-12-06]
Reports/reclamp 07.png

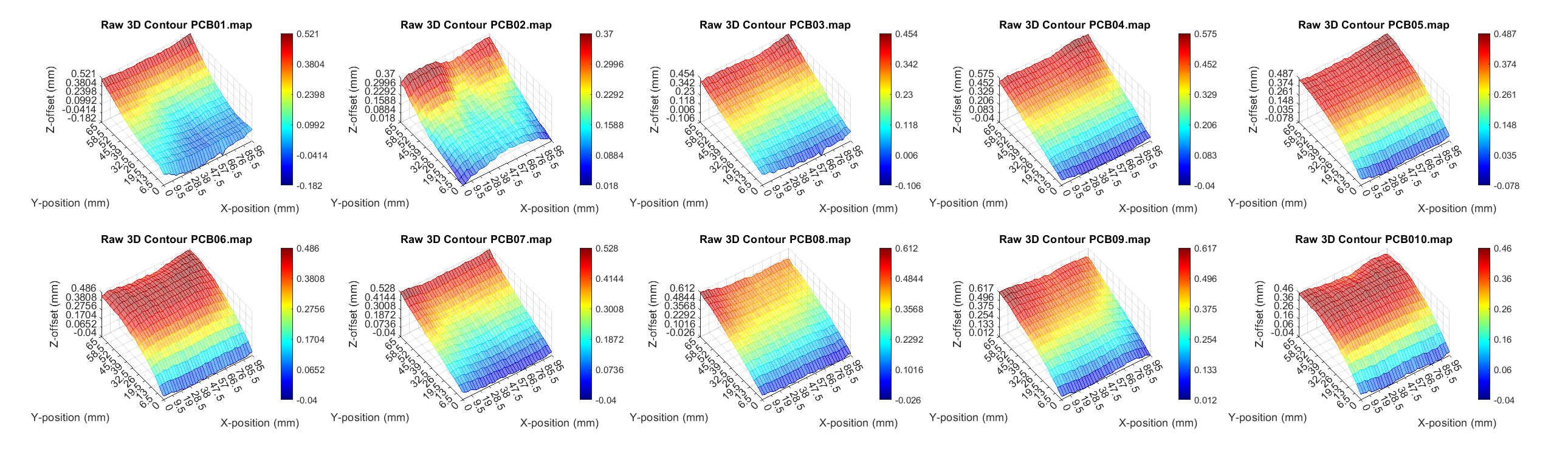
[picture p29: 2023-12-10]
Reports/raw mean set.png

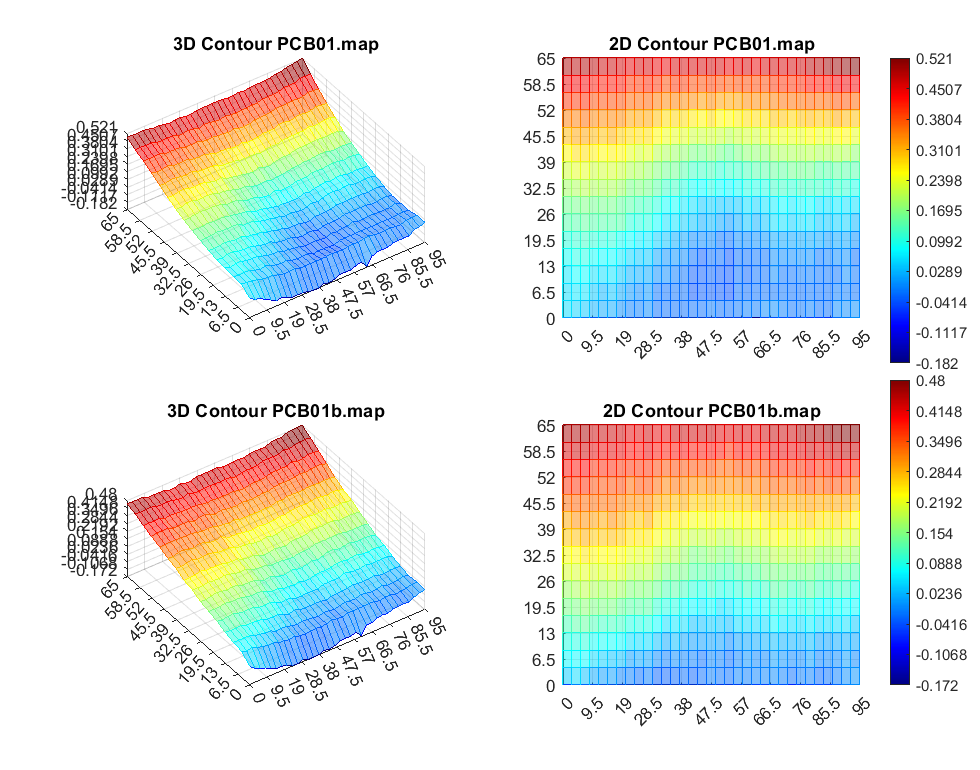
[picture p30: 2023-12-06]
Reports/reclamp 01.png

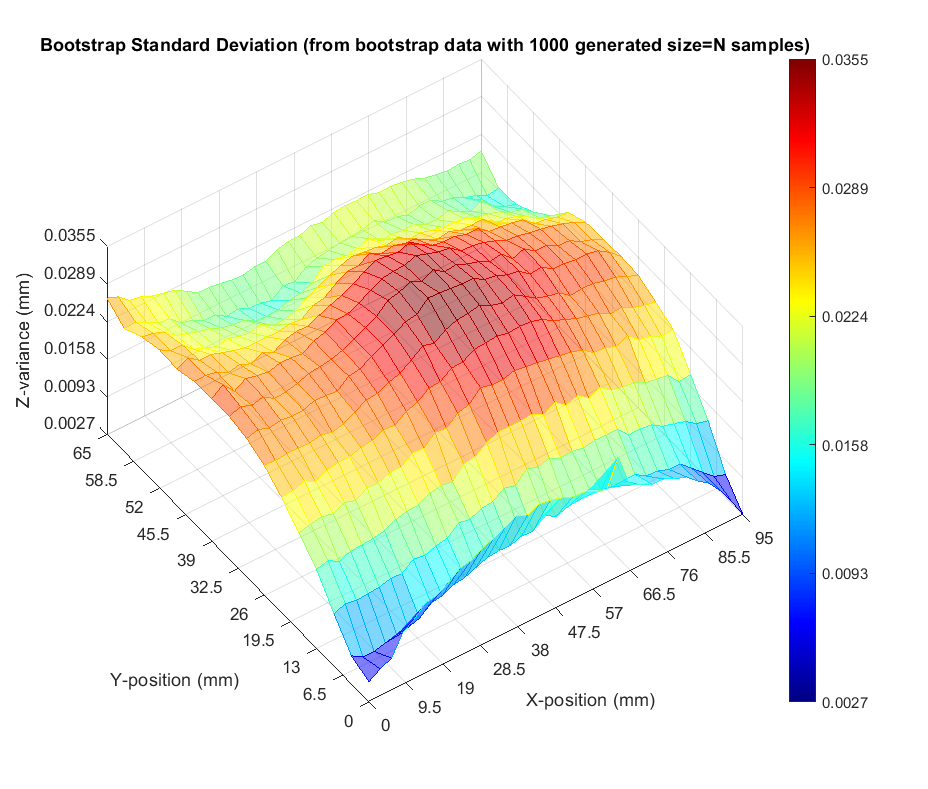
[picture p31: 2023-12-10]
Reports/bootstrap_std_dev.png

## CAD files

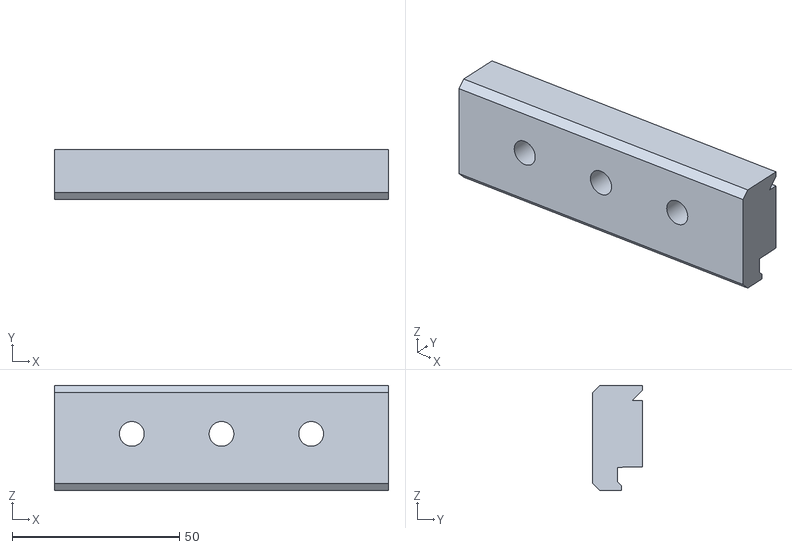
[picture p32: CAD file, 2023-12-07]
100x70mm_Fixture/PCB_Fixture.stl
100.0 x 14.9 x 31.5

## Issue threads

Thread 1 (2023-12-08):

Some configuration results in SVGs lacking holes or other elements

Jbsco, 2023-12-08:
Students reported missing some elements of SVG files at various stages in the described process.
Need to test and verify what could be causing this, and address it in the process.

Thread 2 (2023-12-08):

Sometimes autoplacement does not place components when following the process guide

Jbsco, 2023-12-08:
Some students reported not being able to autoplace components in the PCB editor after moving from the schematic.
Need to test and verify, suspect permissions issues or perhaps project configuration.
Address this in the process readme.

Jbsco, 2023-12-08:
This likely occurs because the PCB Editor needs to update from the Schematic Editor (hotkey "F8").
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
This should run a checker and will report any warnings or errors as well as provide the option to replace existing footprints.

Closed 2023-12-08.

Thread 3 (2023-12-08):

Selection of path elements of SVG in JScut is a lengthy process with complex designs

Jbsco, 2023-12-08:
Students did not want to spend this time working with JScut. Flatcam is ideal for this issue but more testing is needed to ensure we can develop and test the gerber part of the process using our systems and machines.
Many SVG path elements need to be selected. This is how JScut works. This issue is more about looking at alternatives as JScut is superceded by LaserWeb (https://github.com/LaserWeb) and no new features are planned for JScut.

Closed 2023-12-08.

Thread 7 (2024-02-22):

Flat Cam crashes when importing Excellon file using inches

Diego-Sena-Boulder, 2024-02-22:
When using the Flat Cam, you can not load an Excellon file when exported using inches.

Jbsco, 2024-02-23:
Made Readme note of selecting millimeters in commit [1ddb891](https://github.com/Jbsco/PCB_MFG/commit/1ddb891103de92d94346e23f135f9d902ab4144c). This appears to be a bug in some installations of FlatCAM - see possibly related [Denvi/FlatCAM:#3](https://github.com/Denvi/FlatCAM/issues/3). Their issue tracker shows some users have problems with Excellon imports, so this may change with updates in the software.

Closed 2024-02-28.

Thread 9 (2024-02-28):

Primary process readme should link to detailed documentation

Jbsco, 2024-02-28:
Per discussion #8, more detailed sub-processes and explanation of certain software features or tools can be broken out or added in additional markdown documents and link to from the primary process readme. This can be closed upon creation of and linking to any additional markdown readme.

Jbsco, 2024-03-01:
Initialized proposed markdown files in [5f86a6c](https://github.com/Jbsco/PCB_MFG/commit/5f86a6c320385bebcf5c8a92971e496b3bbbe9b9)

Closed 2024-03-01.

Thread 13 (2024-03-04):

Documentation/using_KiCAD.md completion

Jbsco, 2024-03-04:
This issue may be closed by completing documentation for using KiCAD within the context of this process.

Jbsco, 2024-03-21:
Resolved by e5cd490.

Closed 2024-03-21.

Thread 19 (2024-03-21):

Documentation images should be consistent width

Jbsco, 2024-03-21:
Previous implementation using HTML style image linking allowed center-align and also specifying a width to allow images to be consistently sized in documentation - the current markdown implementation does not address this.

See: [ image resize in github flavored markdown ](https://gist.github.com/uupaa/f77d2bcf4dc7a294d109?permalink_comment_id=3561130) for variations on this.

For now solutions appear to be to use the HTML style linking or simply edit images manually to fit, which reduces detail if the image is viewed directly.

Jbsco, 2024-03-21:
Addressed in [a0dd915](https://github.com/Jbsco/PCB_MFG/pull/20/commits/a0dd915ba27c40e9491d03dd99d20f82a8decb51).

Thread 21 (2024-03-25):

FlatCam CutZ Value

chbi4456, 2024-03-25:
"It is recommended to reduce Feedrate Z to 60 (300 may be too high and could cause damage to the board). Adjust Cut Z to a value that will completely drill through the board. If using the provided fixture, there will be ample clearance under the board."

Is there a standard Cut Z that you could add? It would at least be helpful to know what you usually put.

chbi4456, 2024-03-25:
"In FlatCAM, open the Gerber and the Excellon files to add them to the FlatCAM project."

For me, KICad generates several extra excellon and gerber files. It would be helpful to add some directions on which files to use more specifically.

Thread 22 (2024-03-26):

General Comments

AidanMobley, 2024-03-26:
It might be helpful to mention either when you first introduce FlatCam or in the FlatCam tutorial that since FlatCam is always in beta, it often crashes and could require the user to restart their computer to get it to work. Because it crashes so often in my experience it is helpful to save the project as often as possible.

AidanMobley, 2024-03-26:
It may be nice to have a more in-depth KiCad tutorial section which includes the fact that we are milling these boards so the trace width will need to be increased from the default. You may have mentioned this already and I missed it but it is also necessary to mirror everything because the components will be soldered opposite to what the software assumes.

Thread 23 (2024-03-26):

Proposed process changes

kmerickson, 2024-03-26:
For the design process in KICAD, I just have a few suggestions for making PCB design easier:

- Suggest for general PCB design, making traces 0.7 to 1 mm in width for through-hole designs
- for the usual pitch for pins in DIP, suggest maximizing pad size to about 2.25 mm in diameter for easier soldering
- Ensure PCB design fits into copper plate during design
- Suggest deselecting all unnecessary file exports when getting fabrication outputs from KICAD

For the Flatcam process:
- suggest selecting for the preprocessor, GRBL11_no_m6, as this prevented having to delete an M6 command on ever GRBL file before running on candle
- For the drill process, suggest at least a drill depth of at least -3 and a travel Z of about 8, as this seemed to prevent any chance of the drill catching on the board and either breaking or causing damage and seemed to make including a height map for the drill process unnecessary

For Candle:
- Maybe notify that possible Candle may change the Z for some unknown reason when loading in GRBL file or doing the height map, and to double check that. As well as to regularly check spindle collet has not loosened during previous operations
- When designing PCBs that are close to the full size of the board, there seemed be some issue with the height map properly drilling deep enough on the edges. My theory is that the interpolation between points can't reach the very edges

[DSPbufferTutorial2.pdf](https://github.com/Jbsco/PCB_MFG/files/14762290/DSPbufferTutorial2.pdf)
Also I've attached a pdf of a tutorial I made for the DSP class to follow to design an electrode in KICAD. I made this to make a guide more so geared to making easily millable and solderable boards. This tutorial seemed to give everyone enough information in an efficient amount of time to be able to cut out everything not related to CNC mill PCB design in KICAD, and give everyone the tools needed to make any board they would need to make. I have it in word doc format for editing. Let me know if you'd like to include in your github and if a different format is desired. I think you mentioned an HTML mark up format would work better, in which case I would not mind figuring out how to get that done.

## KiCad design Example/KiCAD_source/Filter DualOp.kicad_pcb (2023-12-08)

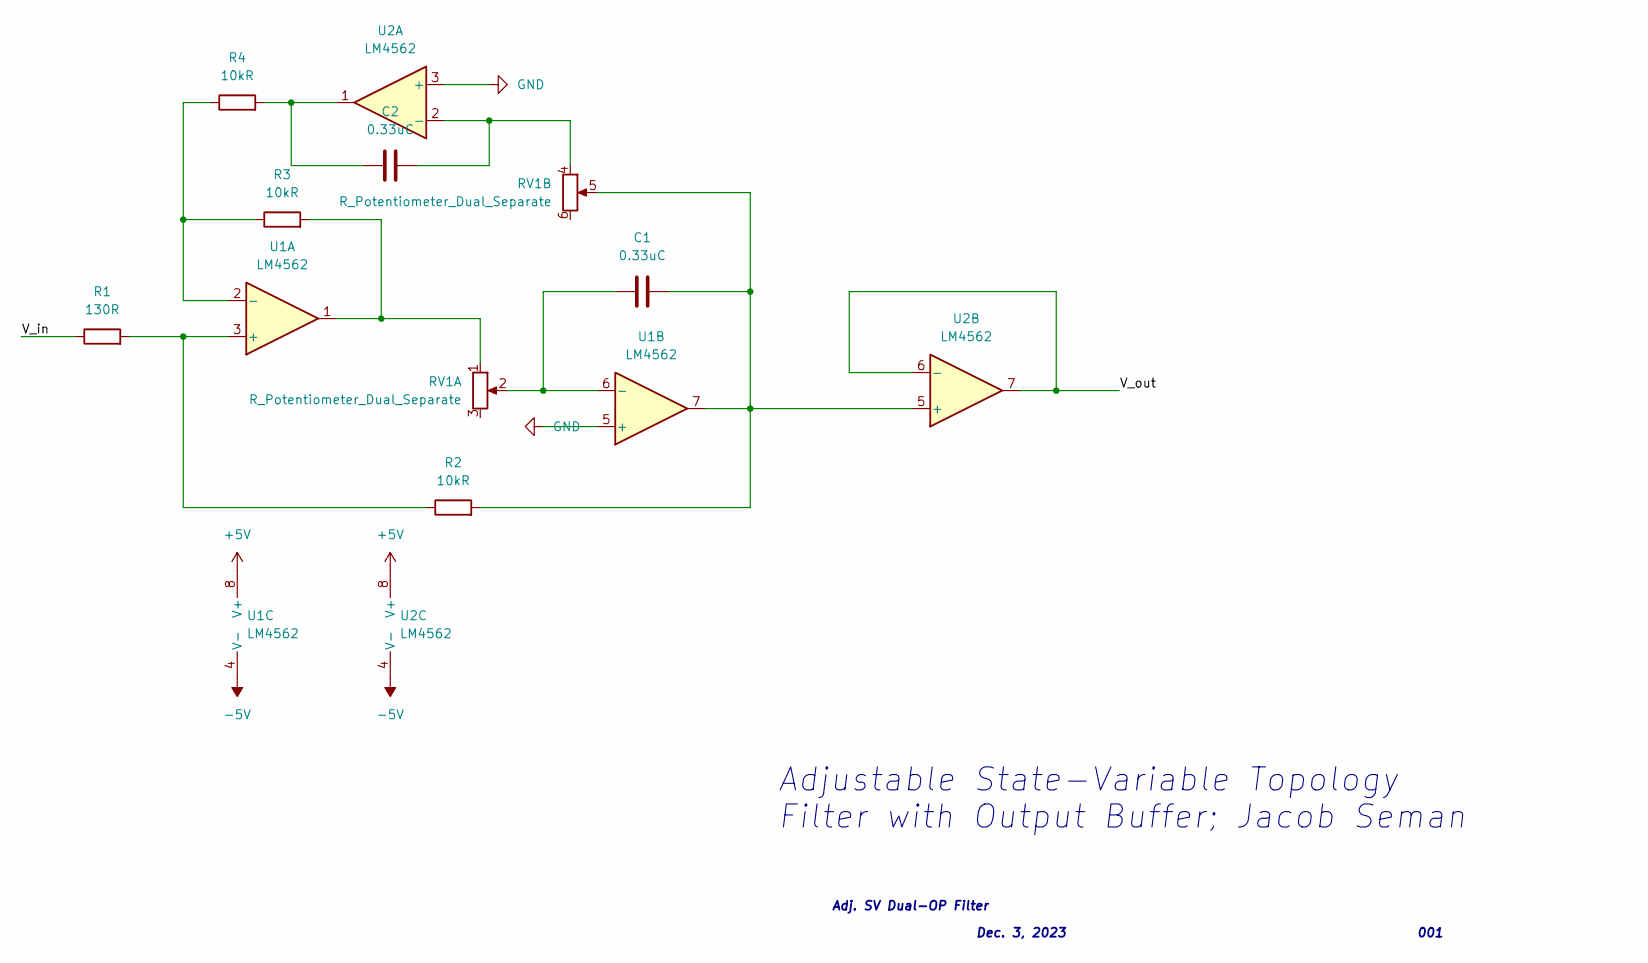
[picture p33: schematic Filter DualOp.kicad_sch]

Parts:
C1, C2: 0.33uC; C_Disc_D5.0mm_W2.5mm_P2.50mm
R1: 130R; R_Axial_DIN0207_L6.3mm_D2.5mm_P2.54mm_Vertical
R2, R3, R4: 10kR; R_Axial_DIN0207_L6.3mm_D2.5mm_P2.54mm_Vertical
RV1: R_Potentiometer_Dual_Separate; Potentiometer_Alps_RK097_Dual_Horizontal
U1, U2: LM4562; DIP-8_W7.62mm

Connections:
+5V: U1.8 (V+), U2.8 (V+)
-5V: U1.4 (V-), U2.4 (V-)
/V_in: R1.1
/V_out: U2.6 (-), U2.7
GND: U1.5 (+), U2.3 (+)
unnamed: C1.1, RV1.2, U1.6 (-)
unnamed: C1.2, R2.2, RV1.5, U1.7, U2.5 (+)
unnamed: C2.1, R4.2, U2.1
unnamed: C2.2, RV1.4, U2.2 (-)
unnamed: R1.2, R2.1, U1.3 (+)
unnamed: R3.1, R4.1, U1.2 (-)
unnamed: R3.2, RV1.1, U1.1

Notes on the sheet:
Dec. 3, 2023
Adj. SV Dual-OP Filter
Adjustable State-Variable Topology Filter with Output Buffer; Jacob Seman
001

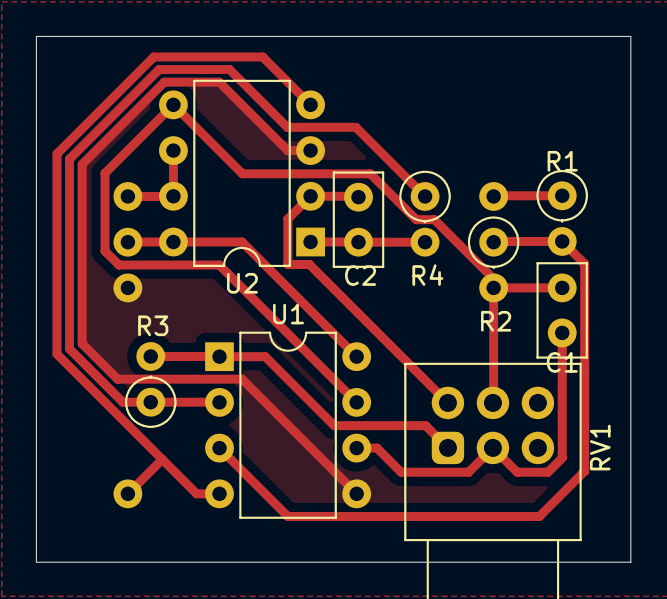
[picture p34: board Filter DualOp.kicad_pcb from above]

Board: 2 copper layers, 33.0 x 29.2 mm, 9 parts (0 on the bottom side), 11 nets.

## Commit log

2023-12-06 initializing repository
    [Filter DualOp.kicad_pcb, Filter DualOp.kicad_sch, tinfoil.map.xlsx]
2023-12-06 init organization
    [Filter DualOp.kicad_pcb, Filter DualOp.kicad_sch]
2023-12-07 organization, included example circuit SPICE simulations
    [Filter DualOp.kicad_pcb, Filter DualOp.kicad_sch, PCB_Fixture.stl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]
2023-12-07 added gerber output and gcode/drill outputs from Flatcam testing
    [Filter DualOp-F_Cu.gbr, Filter DualOp-NPTH.drl, Filter DualOp-PTH.drl]
2023-12-07 updated example project KiCAD project files
    [Filter DualOp.kicad_pcb]
2023-12-07 updated KiCAD project files
    [Filter DualOp.kicad_pcb]
2023-12-08 added FlatCAM files, nearing completion of FlatCAM process testing
    [Filter DualOp-F_Cu.gbr, Filter DualOp-NPTH.drl, Filter DualOp-PTH.drl]
2023-12-08 updated with FlatCAM images
    [Filter DualOp.kicad_pcb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]
2023-12-08 updated example filter design report
2023-12-08 Update README.md, mention of different continuity probe control board labels
2023-12-08 Update README.md, added instruction for switching from schematic to PCB editor
    Addresses #2.
2023-12-08 added KiCAD library depoendencies for Arch Linux install
2023-12-10 added model heightmap "bootModel.map" and additional report materials
    [tinfoil.map.xlsx]
2024-03-01 initializing supplementary markdown documentation for KiCAD, FlatCAM, & Candle per issue #9, discussion #8
2026-02-05 Update KiCad documentation and add images
2026-02-05 Reorganize KiCad documentation
